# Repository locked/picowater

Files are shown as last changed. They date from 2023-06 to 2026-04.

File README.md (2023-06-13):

cd build

cmake -DPICO_BOARD=pico_w -DWIFI_SSID="<wifi>" -DWIFI_PASSWORD="<secret>" -DSERVER_IP="<ip>" -DSERVER_PORT=<port> ..

make

# Sources

https://github.com/iiot2k/pico-lib2/blob/main/src/dev/dev_ds3231/dev_ds3231.c

https://ghubcoder.github.io/posts/awaking-the-pico/

https://github.com/ghubcoder/PicoSleepRtc/blob/master/ds3232rtc.cpp

https://github.com/raspberrypi/pico-examples/blob/master/adc/hello_adc/hello_adc.c

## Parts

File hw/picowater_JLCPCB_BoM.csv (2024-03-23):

Comment | Designator | Footprint | LCSC
220 | R9,R3 | R_0402_1005Metric | C2909336
LED | D4 | LED_0603_1608Metric_Pad1.05x0.95mm_HandSolder | None
1N4007 | D3 | D_SOD-123 | C3018540
TLP160G | U5 | MFSOP6-4_4.4x3.6mm_P1.27mm | C2848498
NCP1117 | U4 | SOT-223-3_TabPin2 | C17314
10u | C4,C5 | C_0805_2012Metric | C88484
SN74HC74N | U2 | SOIC-14_3.9x8.7mm_P1.27mm | C6762
10K | R5,R8,R6,R7 | R_0402_1005Metric | C25744
100nF | C1,C3 | C_0402_1005Metric | C1525
22pF | C2 | C_0402_1005Metric | C1555
34K | R2 | R_0402_1005Metric | C48939
PCF8563T | U3 | SOIC-8_3.9x4.9mm_P1.27mm | C7440
100 | R10 | R_0402_1005Metric | C2906884
JST-PH2 Bat | J6 | JST_PH_S2B-PH-SM4-TB_1x02-1MP_P2.00mm_Horizontal | C295747
100K | R4,R1 | R_0402_1005Metric | C25741
S8050 | Q1 | TSOT-23 | C909746
1A 20V Schottky | D1 | D_SOD-123F | C169527

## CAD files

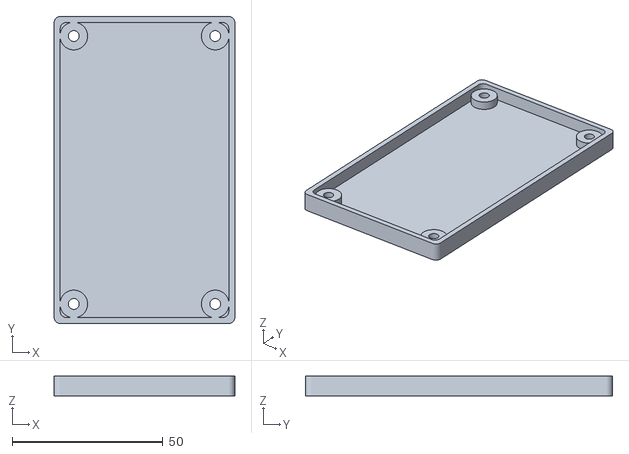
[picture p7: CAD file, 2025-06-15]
case/bottom.stl
60.0 x 102.0 x 6.60

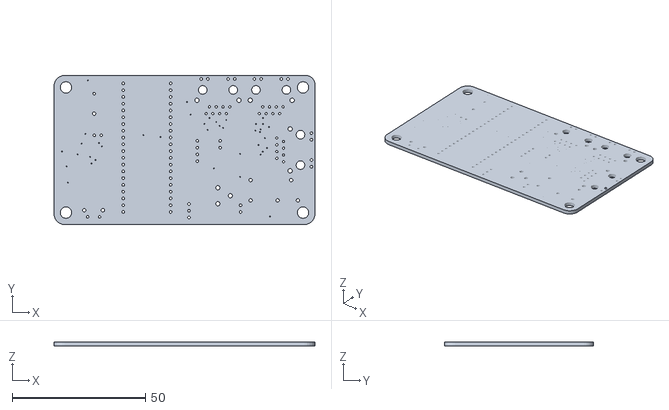
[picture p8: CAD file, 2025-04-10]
hw/picowater.stl
98.0 x 56.0 x 1.51

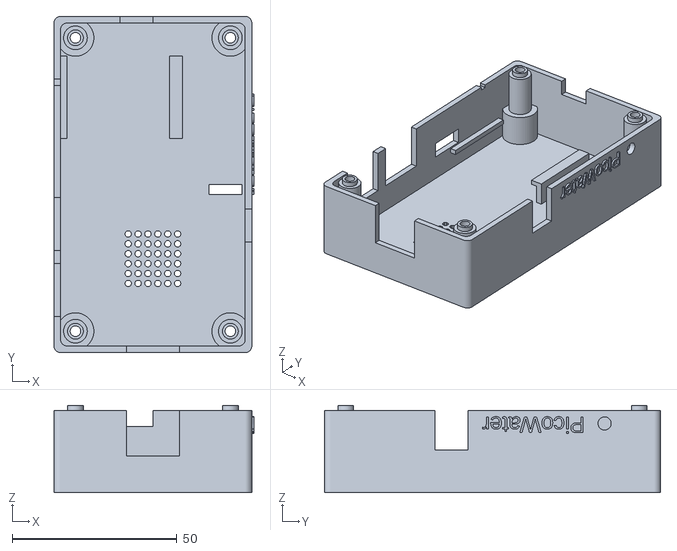
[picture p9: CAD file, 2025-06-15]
case/top.stl
60.7 x 102.0 x 26.5

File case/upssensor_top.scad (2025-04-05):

include <common.scad>;

module case () {
    difference () {
        minkowski() {
            cube([height-round_radius*2, width-round_radius*2, top_depth]);
            cylinder(r=round_radius, h=0.0001);
        }

        translate([round_radius,round_radius,thickness]) minkowski() {
            cube([pcb_height-round_radius*2, pcb_width-round_radius*2, top_depth]);
            cylinder(r=round_radius, h=1);
        }
    }

    // Screw supports
    for (hole = holes) {
        translate([hole[0], hole[1], hole[2]+top_depth])
            cylinder(r=pcb_screw_hole_radius-0.1, h=1.5);
        translate(hole)
            cylinder(r=screw_hole_radius+2, h=top_depth);
        translate(hole)
            cylinder(r=screw_hole_radius+4, h=6);
    }

    translate([pcb_height+thickness, pcb_width-20, top_depth-2])
    rotate([90, 180, 90])
    linear_extrude(thickness/3)
    text("PicoWater", size=6);
}

module screw_holes() {
    for (hole = holes) {
        translate([hole[0], hole[1], -thickness])
            cylinder(r=screw_hole_radius, h=top_depth+thickness+1.5);
        translate([hole[0], hole[1], -bottom_depth+thickness])
            cylinder(r=3.5, h=bottom_depth-thickness+2.5);
    }
}

module rj45() {
    rj45_posx = pcb_height / 2 - rj45[0] / 2;
    rj45_posz = top_depth - rj45[2] + 0.001;
    translate([rj45_posx, -thickness, rj45_posz]) cube(rj45);
}

module debug_hole() {
    debug_posx = pcb_height + thickness;
    debug_posy = pcb_width - 13;
    debug_posz = top_depth - 4;
    translate([debug_posx, debug_posy, debug_posz]) rotate([0, -90, 0]) cylinder(r=2, h=thickness);
}

module airvents() {
    rad = 1;
    posx = pcb_height / 2 - (5*rad*3/2);
    posy = pcb_width / 2 - 5*rad;
    for (i = [0,1,2,3,4,5]) {
        for (j = [0,1,2,3,4,5]) {
            translate([posx + i*rad*3, posy + j*rad*3, 0])
                cylinder(r=rad, h=thickness, $fn=10);
        }
    }
}

module uart() {
    uart_posx = pcb_height - thickness - 2;
    uart_posy = pcb_width - thickness - 10 - 15;
    translate([uart_posx, uart_posy, 0])
        cube([3, 10, thickness]);
}

difference () {
    case();
    screw_holes();
    rj45();
    debug_hole();
    airvents();
    uart();
}

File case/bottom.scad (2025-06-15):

include <common.scad>;

module case () {
    difference () {
        minkowski() {
            cube([height-round_radius*2, width-round_radius*2, bottom_depth]);
            cylinder(r=round_radius, h=pcb_thickness);
        }

        translate([round_radius,round_radius,thickness]) minkowski() {
            cube([pcb_height-round_radius*2, pcb_width-round_radius*2, bottom_depth]);
            cylinder(r=round_radius, h=1);
        }
    }

    // Screw supports
    for (hole = holes) {
        translate(hole)
            cylinder(r=screw_hole_radius+3, h=bottom_depth);
    }
}

module screw_holes() {
    for (hole = holes) {
        translate([hole[0], hole[1], -thickness])
            cylinder(r=screw_hole_radius+0.2, h=bottom_depth+thickness);

        translate([hole[0], hole[1], -bottom_depth+thickness])
            cylinder(r=3.3, h=bottom_depth-thickness+3, $fn=6);
    }
}

difference () {
    case();
    screw_holes();
}

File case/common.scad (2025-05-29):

pcb_width = 98;
pcb_height = 56;
pcb_thickness = 1.6;
pcb_screw_hole_radius = 2.4;	// M4/2-margin

thickness = 2;
round_radius = 2;

width = pcb_width + thickness * 2;	// y
height = pcb_height + thickness * 2;	// x
bottom_depth = 5;	// z
top_depth = 25;		// z

screw_hole_radius = 1.6;	// M2/2
screw_posx = 4.5;
screw_posy = 4.5;

rj45 = [16, thickness*2, 13.8];
powerjack = [10, thickness*2, 12];

$fn = 50;

posx = screw_posx;
posy = screw_posy;
holes = [
    [posx, posy, 0],
    [pcb_height-posx, posy, 0],
    [posx, pcb_width-posy, 0],
    [pcb_height-posx, pcb_width-posy, 0]
];

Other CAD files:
case/top.scad

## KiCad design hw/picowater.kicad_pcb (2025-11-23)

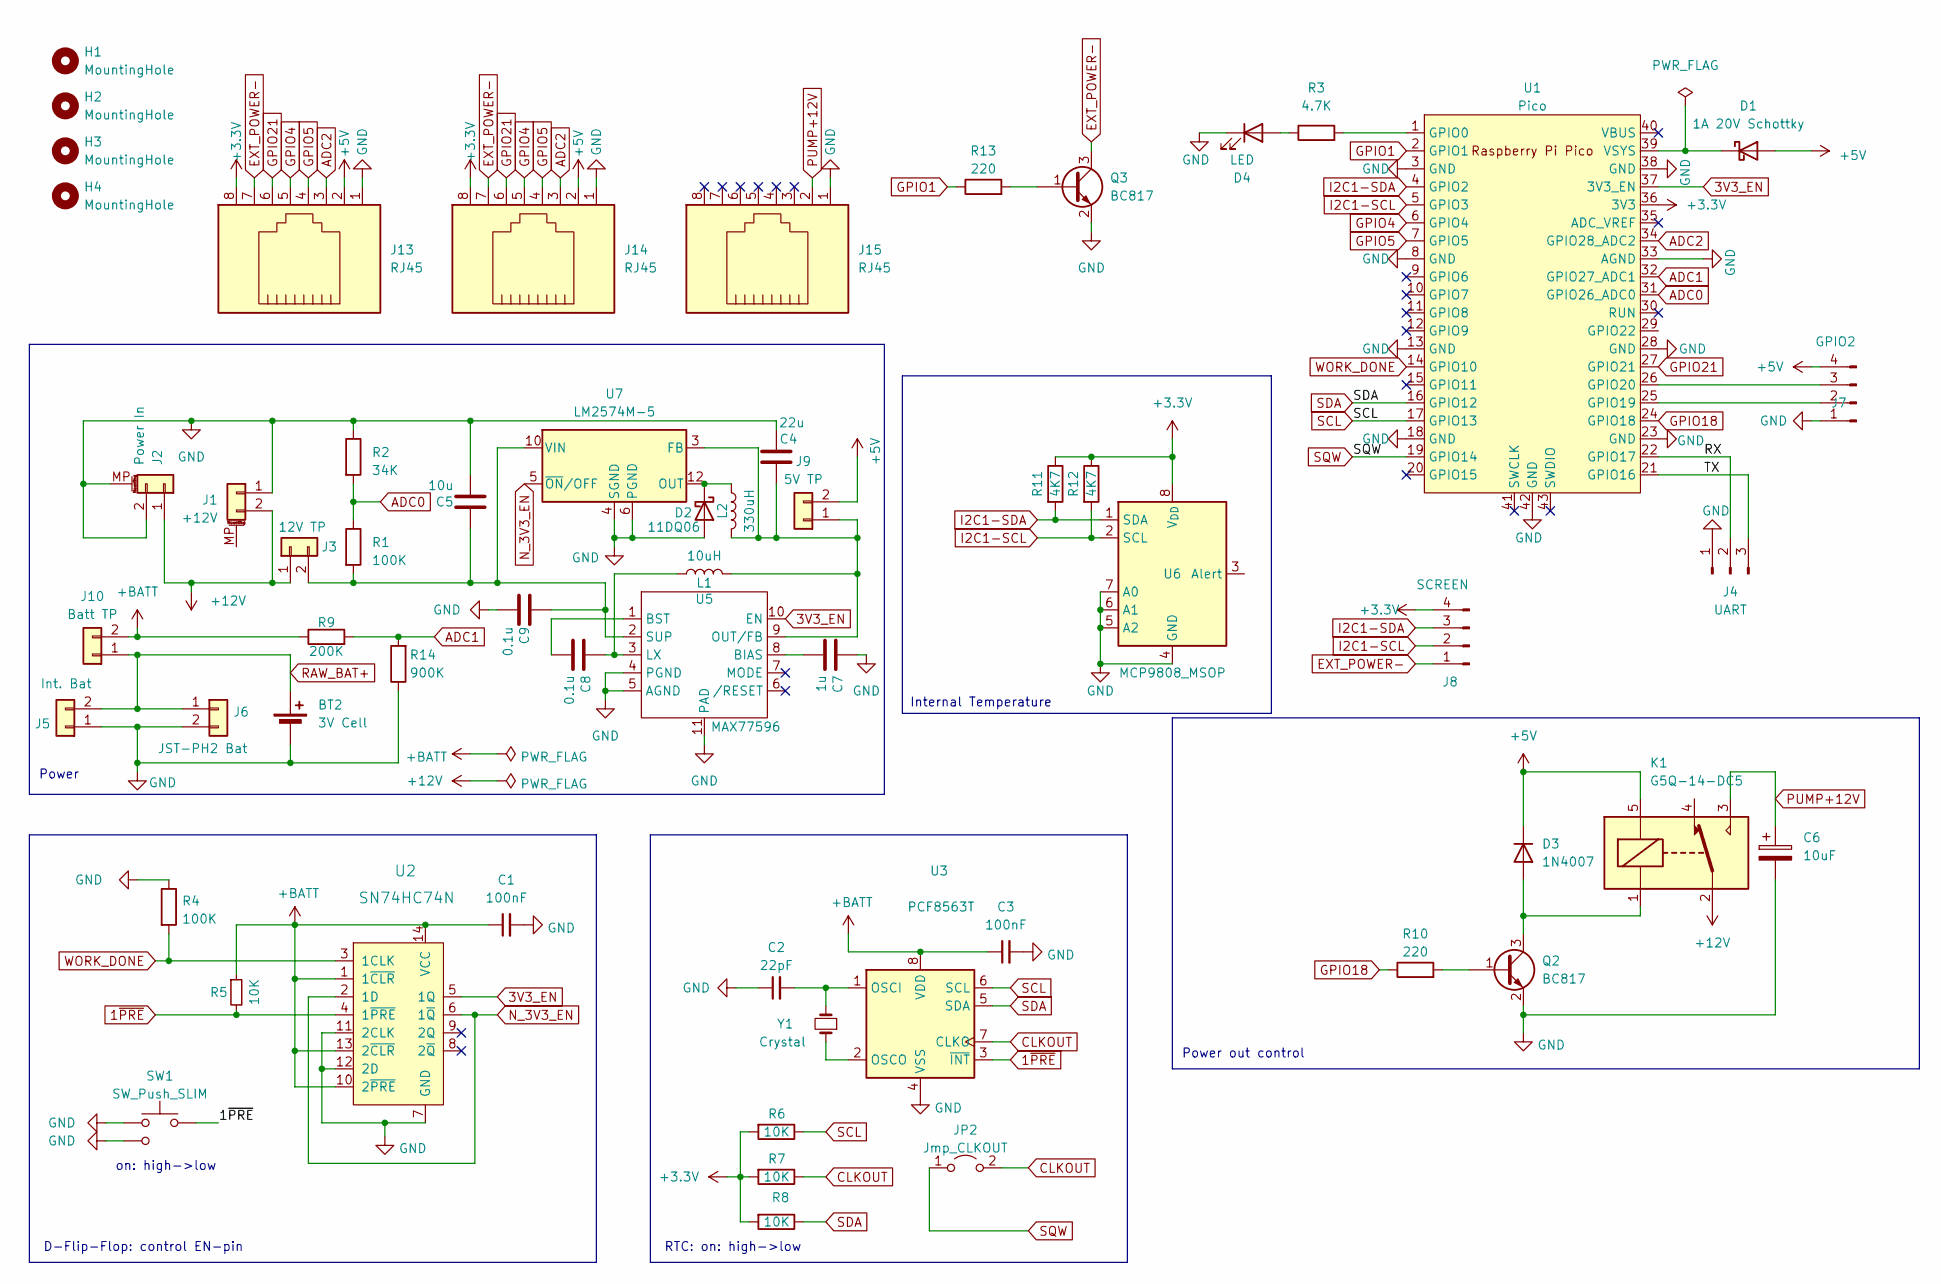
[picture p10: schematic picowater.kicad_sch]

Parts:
BT2: 3V Cell; MPD_BC501SM-TR_custom
C1, C3: 100nF; C_0402_1005Metric; LCSC C1525
C2: 22pF; C_0402_1005Metric; LCSC C1555
C4: 22u; C_0805_2012Metric; LCSC C2846677
C5: 10u; C_0805_2012Metric; LCSC C2846677
C6: 10uF; CP_Radial_D8.0mm_P3.80mm
C7: 1u; C_0603_1608Metric
C8, C9: 0.1u; C_0603_1608Metric
D1: 1A 20V Schottky; D_SOD-123F; LCSC C169527
D2: 11DQ06
D3: 1N4007; D_SOD-123; LCSC C3018540
D4: LED; LED_0603_1608Metric_Pad1.05x0.95mm_HandSolder; JLCPCB Part Number C72041
H1, H2, H3, H4: MountingHole; hole_5mm
J1: +12V; PinSocket_1x02_P2.54mm_Vertical
J2: Power In; BarrelJack_CUI_PJ-102AH_Horizontal
J3: 12V TP; PinHeader_1x02_P2.54mm_Vertical
J4: UART; PinHeader_1x03_P2.54mm_Vertical
J5: Int. Bat; PinHeader_1x02_P2.54mm_Vertical; LCSC C295747
J6: JST-PH2 Bat; JST_PH_S2B-PH-SM4-TB_1x02-1MP_P2.00mm_Horizontal; LCSC C295747
J7: GPIO2; PinHeader_1x04_P2.54mm_Vertical
J8: SCREEN; PinHeader_1x04_P2.54mm_Vertical
J9: 5V TP; PinHeader_1x02_P2.54mm_Vertical
J10: Batt TP; PinHeader_1x02_P2.54mm_Vertical
J13, J14, J15: RJ45; RJ45_BEL_SS74301-00x_Vertical
JP2: Jmp_CLKOUT; SolderJumper-2_P1.3mm_Open_Pad1.0x1.5mm
K1: G5Q-14-DC5; Relay_SPDT_Omron-G5Q-1
L1: 10uH; C_0805_2012Metric
L2: 330uH
Q2, Q3: BC817; SOT-23
R1, R4: 100K; R_0402_1005Metric; LCSC C25741
R2: 34K; R_0402_1005Metric; LCSC C48939
R3: 4.7K; R_0402_1005Metric
R5, R6, R8: 10K; R_0402_1005Metric; LCSC C25744
R7: 10K; R_0805_2012Metric; LCSC C25744
R9: 200K; R_0402_1005Metric
R10, R13: 220; R_0402_1005Metric; LCSC C2909336
R11, R12: 4K7; C_0603_1608Metric; LCSC C25900
R14: 900K; R_0402_1005Metric
SW1: SW_Push_SLIM; SW_Tactile_SPST_Angled_PTS645Vx31-2LFS
U1: Pico; RPi_Pico_SMD_TH
U2: SN74HC74N; SO-14_5.3x10.2mm_P1.27mm; MPN SN74HC74N; Digi-Key_PN 296-1602-5-ND
U3: PCF8563T; SOIC-8_3.9x4.9mm_P1.27mm; LCSC C7440
U5: MAX77596; TDFN-10-EP_2.5mm
U6: MCP9808_MSOP; MSOP-8_3x3mm_P0.65mm; LCSC C129490
U7: LM2574M-5
Y1: Crystal; Crystal_SMD_3215-2Pin_3.2x1.5mm; LCSC C32346

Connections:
1~PRE: R5.2, SW1.2, U2.4 (1~PRE), U3.3 (~INT)
3V3_EN: U1.37 (3V3_EN), U2.5 (1Q), U5.10 (EN)
+3.3V: J8.4, J13.8, J14.8, R6.2, R7.2, R8.2, R11.1, R12.1, U1.36 (3V3), U6.8 (V_{DD})
+5V: D1.2 (A), D3.1 (K), J7.4, J9.2, J13.2, J14.2, K1.5
+12V: J1.2, J2.1, J3.1, K1.2
+BATT: C1.1, C3.1, J10.2, R5.1, R9.1, U2.1 (1~CLR), U2.10 (2~PRE), U2.13 (2~CLR), U2.14 (VCC), U3.8 (VDD)
/RX: J4.2, U1.22 (GPIO17)
/TX: J4.3, U1.21 (GPIO16)
ADC0: R1.1, R2.2, U1.31 (GPIO26_ADC0)
ADC1: R9.2, R14.2, U1.32 (GPIO27_ADC1)
ADC2: J13.3, J14.3, U1.34 (GPIO28_ADC2)
CLKOUT: JP2.2 (B), R7.1, U3.7 (CLKO)
EXT_POWER-: J8.1, J13.7, J14.7, Q3.3 (C)
GND: BT2.2 (-), C1.2, C2.1, C3.2, C4.2, C5.2, C6.2, C7.1, C9.2, D2.2 (A), D4.1 (K), J1.1, J2.2, J2.MP (MountPin), J4.1, J5.1, J6.2, J7.1, J13.1, J14.1, J15.1, Q2.2 (E), Q3.2 (E), R2.1, R4.1, R14.1, SW1.1, SW1.3 (1), U1.3 (GND), U1.8 (GND), U1.13 (GND), U1.18 (GND), U1.23 (GND), U1.28 (GND), U1.33 (AGND), U1.38 (GND), U1.42 (GND), U2.7 (GND), U2.11 (2CLK), U2.12 (2D), U3.4 (VSS), U5.4 (PGND), U5.5 (AGND), U5.11 (PAD), U6.4 (GND), U6.5 (A2), U6.6 (A1), U6.7 (A0), U7.4 (SGND), U7.6 (PGND)
GPIO1: R13.1, U1.2 (GPIO1)
GPIO4: J13.5, J14.5, U1.6 (GPIO4)
GPIO5: J13.4, J14.4, U1.7 (GPIO5)
GPIO18: R10.1, U1.24 (GPIO18)
GPIO21: J13.6, J14.6, U1.27 (GPIO21)
I2C1-SCL: J8.2, R12.2, U1.5 (GPIO3), U6.2 (SCL)
I2C1-SDA: J8.3, R11.2, U1.4 (GPIO2), U6.1 (SDA)
N_3V3_EN: U2.2 (1D), U2.6 (1~Q), U7.5 (~ON/OFF)
unnamed: D1.1 (K), U1.39 (VSYS)
unnamed: D2.1 (K), L2.1, U7.12 (OUT)
unnamed: D3.2 (A), K1.1, Q2.3 (C)
unnamed: D4.2 (A), R3.1
unnamed: C5.1, C9.1, J3.2, R1.2, U5.2 (SUP), U7.10 (VIN)
unnamed: J7.2, U1.25 (GPIO19)
unnamed: J7.3, U1.26 (GPIO20)
unnamed: C4.1, J9.1, L1.2, L2.2, U5.9 (OUT/FB), U7.3 (FB)
unnamed: Q2.1 (B), R10.2
unnamed: Q3.1 (B), R13.2
unnamed: R3.2, U1.1 (GPIO0)
unnamed: C2.2, U3.1 (OSCI), Y1.2
unnamed: U3.2 (OSCO), Y1.1
unnamed: C7.2, U5.8 (BIAS)
unnamed: C8.2, U5.1 (BST)
unnamed: C8.1, L1.1, U5.3 (LX)
PUMP+12V: C6.1, J15.2, K1.3
RAW_BAT+: BT2.1 (+), J5.2, J6.1, J10.1
SCL: R6.1, U1.17 (GPIO13), U3.6 (SCL)
SDA: R8.1, U1.16 (GPIO12), U3.5 (SDA)
SQW: JP2.1 (A), U1.19 (GPIO14)
WORK_DONE: R4.2, U1.14 (GPIO10), U2.3 (1CLK)

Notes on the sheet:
Power
on: high->low
Power out control
RTC: on: high->low
D-Flip-Flop: control EN-pin
Internal Temperature

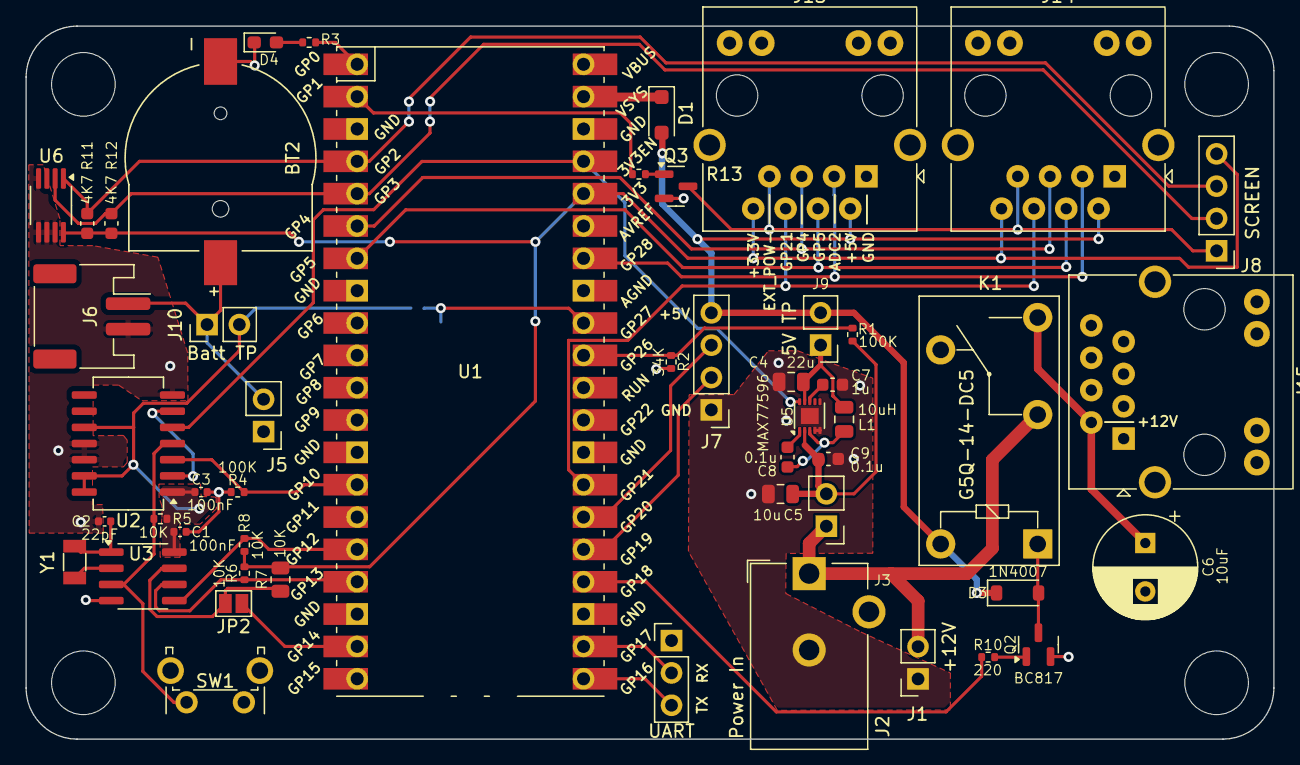
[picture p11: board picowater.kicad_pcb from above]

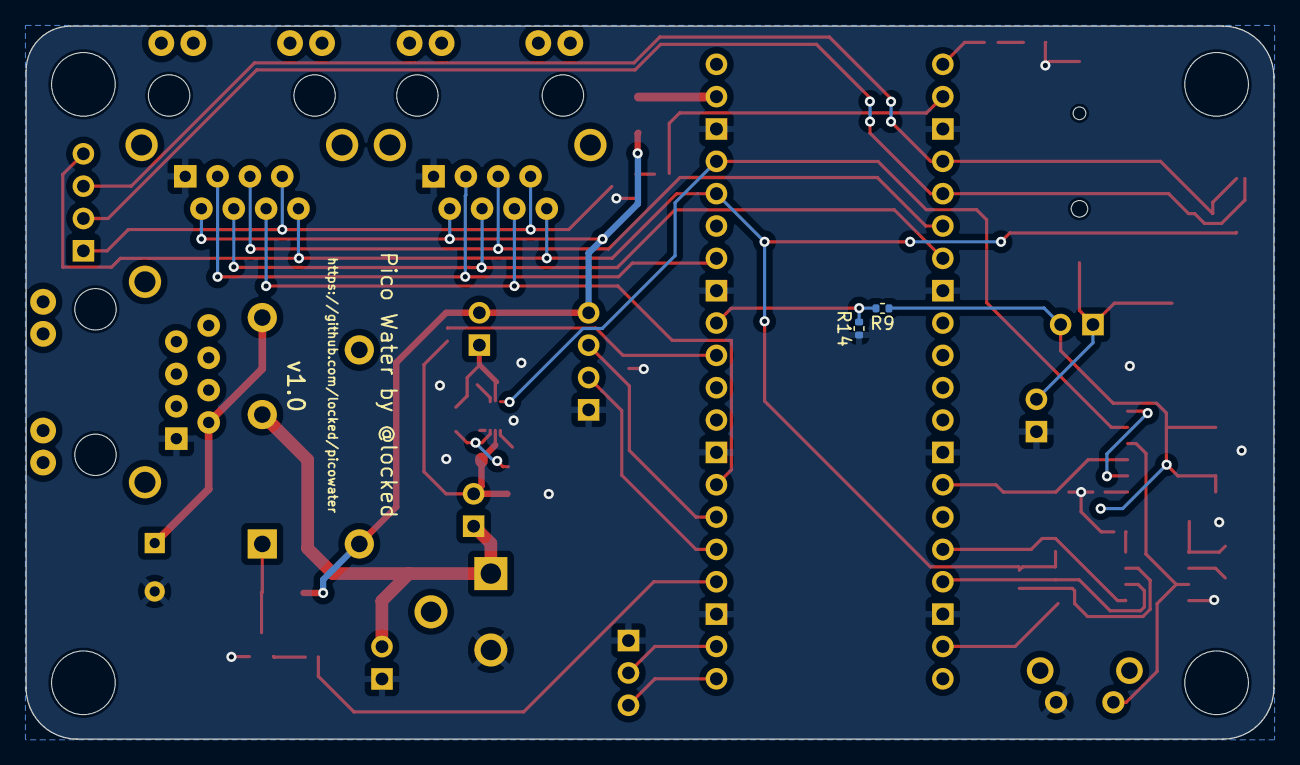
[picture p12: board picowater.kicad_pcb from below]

Board: 2 copper layers, 98.0 x 56.0 mm, 56 parts (2 on the bottom side), 43 nets.

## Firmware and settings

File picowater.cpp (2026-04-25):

#include <stdlib.h>
#include <stdio.h>
#include <string.h>
#include <time.h>

#include "pico/stdlib.h"
#include "pico/sleep.h"

#include "hardware/rtc.h"
#include "hardware/uart.h"
#include "hardware/gpio.h"
#include "hardware/adc.h"
#include "hardware/i2c.h"
#include "hardware/watchdog.h"

#include "pico/util/datetime.h"

#include "hardware/clocks.h"
#include "hardware/rosc.h"
#include "hardware/structs/scb.h"

#include "wifi.h"

#include "ssd1306.h"
#include "acme_5_outlines_font.h"
#include "bubblesstandard_font.h"
#include "crackers_font.h"
#include "BMSPA_font.h"

#include "pcf8563/pcf8563.h"
#include "mcp9808/mcp9808.h"

#include "network.h"

#include "picowater.h"


int pump_force_ms;
bool wakeup_everymin;

int dist;
float batlvl;
float batlvl2;
float systemp;


void _i2c_init(i2c_inst_t* i2c, uint32_t sda, uint32_t scl, uint32_t baudrate) {
	uint8_t idx = (i2c == i2c0) ? 0 : 1;

	i2c_init(i2c, baudrate);

	// init pins
	gpio_set_function(sda, GPIO_FUNC_I2C);
	gpio_set_function(scl, GPIO_FUNC_I2C);

	gpio_pull_up(sda);
	gpio_pull_up(scl);
}



void blink(int count, int delay) {
	int i = 0;
	gpio_put(LED_PIN, 0);
	while (i < count) {
		gpio_put(LED_PIN, 1);
		sleep_ms(20);
		gpio_put(LED_PIN, 0);
		sleep_ms(delay);
		i++;
	}
}


void setup_i2c() {
	i2c_init(i2c1, 400000);
	gpio_set_function(SCREEN_SDA_PIN, GPIO_FUNC_I2C);
	gpio_set_function(SCREEN_SCL_PIN, GPIO_FUNC_I2C);
	gpio_pull_up(SCREEN_SDA_PIN);
	gpio_pull_up(SCREEN_SCL_PIN);
}


void setup_screen(ssd1306_t *disp) {
	disp->external_vcc = false;
	ssd1306_init(disp, 128, 64, 0x3C, i2c1);
	ssd1306_clear(disp);
}


void setup_adc() {
	uart_puts(UART_ID, "== Setup ADC ==\r\n");
	uart_default_tx_wait_blocking();
	printf("== Setup ADC ==\n");
	adc_init();
	// Make sure GPIO is high-impedance, no pullups etc
	adc_gpio_init(BATTERY_ADC_PIN);
	adc_gpio_init(BATTERY2_ADC_PIN);
	adc_gpio_init(HUMIDITY_ADC_PIN);
}


void setup_rtc_pcf() {
	uart_puts(UART_ID, "== RTC PCF8563 init ==\r\n");
	uart_default_tx_wait_blocking();
	printf("RTC PCF8563 init\n");

	//_i2c_init(I2C_RTC_PORT, RTC_SDA_PIN, RTC_SCL_PIN, 100000);
	i2c_init(I2C_RTC_PORT, 100 * 1000);
	gpio_set_function(RTC_SDA_PIN, GPIO_FUNC_I2C);
	gpio_set_function(RTC_SCL_PIN, GPIO_FUNC_I2C);
	gpio_pull_up(RTC_SDA_PIN);
	gpio_pull_up(RTC_SCL_PIN);

	pcf8563_set_i2c(I2C_RTC_PORT);
	printf("[picoclock] pcf8563_set_i2c OK\r\n");

	time_struct _dt = pcf8563_getDateTime();
	if (!_dt.volt_low) {
		printf("RTC not initialized [%d] %d-%d-%d %d:%d:%d\n", _dt.century, _dt.year, _dt.month, _dt.day, _dt.hour, _dt.min, _dt.sec);

		// Fetch date
		//network_update();
	}
}

void rtc_pcf_sleep() {
	printf("Will set ALARM\n");
	uart_default_tx_wait_blocking();
	sleep_ms(500);

	time_struct dt = pcf8563_getDateTime();
	int min = dt.min;
	int hour = dt.hour;
	int day = dt.day;
	int weekday = dt.weekday;

	if (wakeup_everymin) {
		min += 1;
		if (min > 59) {
			hour += 1;
			min -= 60;
		}
	} else {
		hour += 1;
	}
	if (hour > 23) {
		day += 1;
		weekday += 1;
		hour -= 24;
	}
	if (day > 30) {
		day -= 30;
	}
	if (weekday > 6) {
		weekday = 0;
	}

	printf("Set ALARM to day %02d at %02d:%02d weekday:%d\n", day, hour, min, weekday);
	uart_default_tx_wait_blocking();
	sleep_ms(100);

	pcf8563_setAlarm(min, hour, day, weekday);
	pcf8563_enableAlarm();

	// shutdown PI through SN74HC74N
	blink(2, 500);
	printf("SHUTDOWN\n");
	uart_default_tx_wait_blocking();
	sleep_ms(100);
	gpio_put(RTC_WORK_DONE_PIN, 1);
}


void setup_humidity() {
	gpio_init(HUMIDITY_POWER_PIN);
	gpio_set_dir(HUMIDITY_POWER_PIN, GPIO_OUT);
}


void setup_distance() {
	gpio_init(DISTANCE_ECHO_PIN);
	gpio_init(DISTANCE_TRIG_PIN);
	gpio_set_dir(DISTANCE_TRIG_PIN, GPIO_OUT);
	gpio_set_dir(DISTANCE_ECHO_PIN, GPIO_IN);
	gpio_pull_down(DISTANCE_ECHO_PIN);
}

int measure_distance() {
	absolute_time_t pulse_start, pulse_end;
	uint32_t loop_count = 0;
	uint32_t loop_count2 = 0;
	gpio_put(DISTANCE_TRIG_PIN, 0);
	sleep_ms(200);
	gpio_put(DISTANCE_TRIG_PIN, 1);
	sleep_us(10);
	gpio_put(DISTANCE_TRIG_PIN, 0);
	while (gpio_get(DISTANCE_ECHO_PIN) == 0) {
		if (loop_count++ > 3000000) {
			printf("exit loop\r\n");
			break;
		}
	}
	//tight_loop_contents();
	pulse_start = get_absolute_time();
	while (gpio_get(DISTANCE_ECHO_PIN) == 1) {
		sleep_us(1);
		loop_count2++;
		if (loop_count2 > 30000) {
			printf("exit loop2\r\n");
			break;
		}
	}
	pulse_end = get_absolute_time();
	int64_t pulse_duration = absolute_time_diff_us(pulse_start, pulse_end);
	int distance = pulse_duration / 29 / 2;
	char buf[100] = "";
	sprintf(buf, "distance:[%d] loop_count:[%u/%u] pulse_start:[%u] pulse_end:[%u] pulse_duration:[%l]\r\n", distance, loop_count, loop_count2, pulse_start, pulse_end, pulse_duration);
	uart_puts(UART_ID, buf);
	uart_default_tx_wait_blocking();
	printf(buf);
	return distance;
}

void add_water(datetime_t *dt) {
	char buf[100] = "";
	// Read Main Battery ADC
	adc_select_input(0); // Select ADC input 0 (GPIO26)
	const float conversion_factor = 3.3f / (1 << 12);
	batlvl = adc_read() * conversion_factor;

	// Read Battery2 ADC
	adc_select_input(1); // Select ADC input 1 (GPIO27)
	batlvl2 = adc_read() * conversion_factor;

	// Read Humidity ADC
	/*adc_select_input(2); // Select ADC input 2 (GPIO28)
	gpio_put(HUMIDITY_POWER_PIN, 1);
	sleep_ms(10);
	float humidity_result = adc_read() * conversion_factor;
	gpio_put(HUMIDITY_POWER_PIN, 0);
	sprintf(buf, "ADC Battery:[%fV] Battery2:[%fV] Humidity:[%fV]\r\n", batlvl, batlvl2, humidity_result);
	uart_puts(UART_ID, buf);
	uart_default_tx_wait_blocking();
	printf(buf);*/

	// Temperature
	systemp = mcp9808_get_temperature();

	watchdog_update();
	// Water level
	dist = measure_distance();
	if (dist <= 0) {
		printf("Failed getting distance:[%d]\r\n", dist);
		sleep_ms(1000);
		dist = measure_distance();
	}
	sprintf(buf, "DIST:[%u]\r\n", dist);
	uart_puts(UART_ID, buf);
	uart_default_tx_wait_blocking();
	printf(buf);
	watchdog_update();

	// shutdown power for ext devices (except pump)
	gpio_put(EXT_POWER_PIN, 0);

	// Decide to activate pump or not
	int activate_pump_ms = 0;
	// Every hour:
	//int factor = 1;
	//if (dt->hour >= 8 && dt->hour <= 21) {
	// Morning and evening:
	/*int factor = 2;
	if (dt->hour == 8 || dt->hour == 21) {
		sprintf(buf, "In time for pump:[%d]\r\n", dt->hour);
		uart_puts(UART_ID, buf);
		uart_default_tx_wait_blocking();
		printf(buf);
		if (dist >= 1 && dist <= 18) {
			sprintf(buf, "Enough water for pump:[%d]\r\n", dist);
			uart_puts(UART_ID, buf);
			uart_default_tx_wait_blocking();
			printf(buf);
			if (humidity_result >= 2.5) {
				// Very dry
				activate_pump_ms = 10000 * factor;
			} else if (humidity_result >= 2.25) {
				// A bit dry
				activate_pump_ms = 7500 * factor;
			} else if (humidity_result >= 1.75) {
				// Not very dry
				activate_pump_ms = 5000 * factor;
			}
		}
	}*/

	//bool wakeup_everymin = false;

	// WIFI
	bool enable_wifi = true;
	if (enable_wifi) {
		blink(3, 100);
		sleep_ms(1000);

		int network_rc = network_update();
		watchdog_update();

		printf("wakeup_everymin:[%d] activate_pump_ms:[%d] network_rc:[%d]\n", wakeup_everymin, activate_pump_ms, network_rc);
		if (network_rc > 0) {
			// Network failed, check if manual failsafe necessary
			activate_pump_ms = 0;
			if ((dt->hour == 7 || dt->hour == 20) && batlvl > 2.9 && dist > 10) {
				// It's time AND we have enough battery and water, activate pump
				activate_pump_ms = 10000;
			}
		} else {
			activate_pump_ms = pump_force_ms;
		}
	}


	// Pump activation
	if (activate_pump_ms > 0) {
		blink(5, 100);

		sprintf(buf, "Activate pump for [%dms]\r\n", activate_pump_ms);
		uart_puts(UART_ID, buf);
		uart_default_tx_wait_blocking();
		printf(buf);

		gpio_put(PUMP_PIN, 1);
		// Loop because we want to update watchdog every 500ms
		for (int sum_ms = 0; sum_ms<activate_pump_ms; sum_ms+=500) {
			sleep_ms(500);
			watchdog_update();
		}
		gpio_put(PUMP_PIN, 0);
	}
	watchdog_update();

	printf("add_water DONE\n");
}


int main() {
	char buf[50] = "";

	uart_init(UART_ID, BAUD_RATE);
	gpio_set_function(UART_TX_PIN, GPIO_FUNC_UART);
	gpio_set_function(UART_RX_PIN, GPIO_FUNC_UART);

	uint scb_orig = scb_hw->scr;
	uint clock0_orig = clocks_hw->sleep_en0;
	uint clock1_orig = clocks_hw->sleep_en1;

	gpio_init(LED_PIN);
	gpio_set_dir(LED_PIN, GPIO_OUT);
	gpio_put(LED_PIN, 1);

	gpio_init(RTC_WORK_DONE_PIN);
	gpio_set_dir(RTC_WORK_DONE_PIN, GPIO_OUT);
	gpio_put(RTC_WORK_DONE_PIN, 0);

	gpio_init(EXT_POWER_PIN);
	gpio_set_dir(EXT_POWER_PIN, GPIO_OUT);
	gpio_put(EXT_POWER_PIN, 1);

	gpio_init(PUMP_PIN);
	gpio_set_dir(PUMP_PIN, GPIO_OUT);
	gpio_put(PUMP_PIN, 0);

	uart_puts(UART_ID, "==START==\r\n");
	uart_default_tx_wait_blocking();
	stdio_init_all();
	printf("==START==\n");

	gpio_pull_up(RTC_SQW_PIN);

	// Setup I2C
	setup_i2c();

	//ssd1306_t disp;
	//setup_screen(&disp);
	//ssd1306_draw_line(&disp, 0, 0, 127, 0);
	//sprintf(buf, "start");
	//ssd1306_draw_string_with_font(&disp, 1, 1, 2, acme_font, buf);
	//ssd1306_show(&disp);

	watchdog_enable(10000, false);

	// Setup humidity sensor
	setup_humidity();

	// Init water level
	setup_distance();

	// ADC
	setup_adc();

	// RTC
	setup_rtc_pcf();
	watchdog_update();

	gpio_put(LED_PIN, 0);

	datetime_t dt;
	char datetime_buf[256];
	char *datetime_str = &datetime_buf[0];
	uart_puts(UART_ID, "Start loop\r\n");
	uart_default_tx_wait_blocking();
	while (1) {
		//blink(1, 100);
		//sleep_ms(1000);

		add_water(&dt);

		printf("sleep\n");
		rtc_pcf_sleep();
		sleep_ms(500);
		uint32_t sleep_for = wakeup_everymin ? 60000 : 3600000;
		printf("sleep done (should never be seen) => start work around with sleep(%d)\n", sleep_for);
		sleep_ms(sleep_for);
	}
	return 0;
}

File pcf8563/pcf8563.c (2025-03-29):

#include "pcf8563.h"

#include "pico/stdlib.h"


uint8_t constrain(uint8_t x, uint8_t a, uint8_t b){
  if (x < a) {
    return a;
  }
  if (x > b) {
    return b;
  }

  return x;
}


/*
 * Wire abstraction
 */

i2c_inst_t *pcf8563_i2c;

void pcf8563_set_i2c(i2c_inst_t *i2c) {
	pcf8563_i2c = i2c;
}


/* Private internal functions, but useful to look at if you need a similar func. */
uint8_t pcf8563_decToBcd(uint8_t val) {
    return ( (val/10*16) + (val%10) );
}

uint8_t pcf8563_bcdToDec(uint8_t val) {
    return ( (val/16*10) + (val%16) );
}

void pcf8563_zeroClock() {
    uint8_t txBuffer[256];
    uint32_t usedTxBuffer;
    txBuffer[usedTxBuffer++] = (uint8_t)0x0;        // start address

    txBuffer[usedTxBuffer++] = (uint8_t)0x0;     //control/status1
    txBuffer[usedTxBuffer++] = (uint8_t)0x0;     //control/status2
    txBuffer[usedTxBuffer++] = (uint8_t)0x00;    //set seconds to 0 & VL to 0
    txBuffer[usedTxBuffer++] = (uint8_t)0x00;    //set minutes to 0
    txBuffer[usedTxBuffer++] = (uint8_t)0x00;    //set hour to 0
    txBuffer[usedTxBuffer++] = (uint8_t)0x01;    //set day to 1
    txBuffer[usedTxBuffer++] = (uint8_t)0x00;    //set weekday to 0
    txBuffer[usedTxBuffer++] = (uint8_t)0x81;    //set month to 1, century to 1900
    txBuffer[usedTxBuffer++] = (uint8_t)0x00;    //set year to 0
    txBuffer[usedTxBuffer++] = (uint8_t)0x80;    //minute alarm value reset to 00
    txBuffer[usedTxBuffer++] = (uint8_t)0x80;    //hour alarm value reset to 00
    txBuffer[usedTxBuffer++] = (uint8_t)0x80;    //day alarm value reset to 00
    txBuffer[usedTxBuffer++] = (uint8_t)0x80;    //weekday alarm value reset to 00
    txBuffer[usedTxBuffer++] = (uint8_t)SQW_32KHZ; //set SQW to default, see: setSquareWave
    txBuffer[usedTxBuffer++] = (uint8_t)0x0;     //timer off

    if (i2c_write_blocking_until(pcf8563_i2c, RTCC_ADDR, txBuffer, usedTxBuffer, false, make_timeout_time_ms(1000)) == PICO_ERROR_GENERIC){
		printf("pcf8563_zeroClock write error\n");
    }
}

void pcf8563_clearStatus() {
    uint8_t txBuffer[256];
    uint32_t usedTxBuffer;
    txBuffer[usedTxBuffer++] = (uint8_t)0x0;
    txBuffer[usedTxBuffer++] = (uint8_t)0x0;                 //control/status1
    txBuffer[usedTxBuffer++] = (uint8_t)0x0;                 //control/status2
    if (i2c_write_blocking_until(pcf8563_i2c, RTCC_ADDR, txBuffer, usedTxBuffer, false, make_timeout_time_ms(1000)) == PICO_ERROR_GENERIC){
		printf("pcf8563_clearStatus write error\n");
    }
}

/*
* Read status byte
*/
uint8_t pcf8563_readStatus2() {
    time_struct t = pcf8563_getDateTime();
    return t.status2;
}

void pcf8563_clearVoltLow(void) {
    time_struct t = pcf8563_getDateTime();
    // Only clearing is possible on device (I tried)
    pcf8563_setDateTime(t.day, t.weekday, t.month,
                t.century, t.year, t.hour,
                t.min, t.sec);
}


/*
* Atomicly read all device registers in one operation
*/
time_struct pcf8563_getDateTime(void) {
    time_struct t;

    /* Start at beginning, read entire memory in one go */
    uint8_t txBuffer[256];
    uint32_t usedTxBuffer;
    txBuffer[usedTxBuffer++] = (uint8_t)RTCC_STAT1_ADDR;
    if (i2c_write_blocking_until(pcf8563_i2c, RTCC_ADDR, txBuffer, usedTxBuffer, false, make_timeout_time_ms(1000)) == PICO_ERROR_GENERIC){
		printf("pcf8563_getDateTime write error\r\n");
		return t;
    }

    /* As per data sheet, have to read everything all in one operation */
    uint8_t readBuffer[16] = {0};
	int ret = i2c_read_blocking_until(pcf8563_i2c, RTCC_ADDR, readBuffer, 16, false, make_timeout_time_ms(1000));
	if (ret == PICO_ERROR_GENERIC) {
		printf("pcf8563_getDateTime read error\r\n");
		return t;
	}
    //for (uint8_t i=0; i < 16; i++)
    //    readBuffer[i] = _i2c.read();

    // status bytes
    t.status1 = readBuffer[0];
    t.status2 = readBuffer[1];

    // time bytes
    //0x7f = 0b01111111
    t.volt_low = readBuffer[2] & RTCC_VLSEC_MASK;  //VL_Seconds
    t.sec = pcf8563_bcdToDec(readBuffer[2] & ~RTCC_VLSEC_MASK);
    t.min = pcf8563_bcdToDec(readBuffer[3] & 0x7f);
    //0x3f = 0b00111111
    t.hour = pcf8563_bcdToDec(readBuffer[4] & 0x3f);
    if(pcf8563_bcdToDec(readBuffer[4] & 0x3f) > 12) {
        t.hour12 = pcf8563_bcdToDec(readBuffer[4] & 0x3f) - 12;
        t.am = false;
    } else {
        t.hour12 = t.hour;
        t.am = true;
    }
    
    // date bytes
    //0x3f = 0b00111111
    t.day = pcf8563_bcdToDec(readBuffer[5] & 0x3f);
    //0x07 = 0b00000111
    t.weekday = pcf8563_bcdToDec(readBuffer[6] & 0x07);
    //get raw month data uint8_t and set month and century with it.
    t.month = readBuffer[7];
    if (t.month & RTCC_CENTURY_MASK)
        t.century = true;
    else
        t.century = false;
    //0x1f = 0b00011111
    t.month = t.month & 0x1f;
    t.month = pcf8563_bcdToDec(t.month);
    t.year = pcf8563_bcdToDec(readBuffer[8]);

    // alarm bytes
    t.alarm_min = readBuffer[9];
    if(0b10000000 & t.alarm_min)
        t.alarm_min = RTCC_NO_ALARM;
    else
        t.alarm_min = pcf8563_bcdToDec(t.alarm_min & 0b01111111);
    t.alarm_hour = readBuffer[10];
    if(0b10000000 & t.alarm_hour)
        t.alarm_hour = RTCC_NO_ALARM;
    else
        t.alarm_hour = pcf8563_bcdToDec(t.alarm_hour & 0b00111111);
    t.alarm_day = readBuffer[11];
    if(0b10000000 & t.alarm_day)
        t.alarm_day = RTCC_NO_ALARM;
    else
        t.alarm_day = pcf8563_bcdToDec(t.alarm_day  & 0b00111111);
    t.alarm_weekday = readBuffer[12];
    if(0b10000000 & t.alarm_weekday)
        t.alarm_weekday = RTCC_NO_ALARM;
    else
        t.alarm_weekday = pcf8563_bcdToDec(t.alarm_weekday  & 0b00000111);

    // CLKOUT_control 0x03 = 0b00000011
    t.squareWave = readBuffer[13] & 0x03;

    // timer bytes
    t.timer_control = readBuffer[14] & 0x03;
    t.timer_value = readBuffer[15];  // current value != set value when running

	return t;
}
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

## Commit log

2023-05-28 add kicad project
    [picowater.kicad_pcb, picowater.kicad_sch]
2023-05-28 update resistor
2023-06-03 add pico code (from pico_w example library)
2023-06-03 use lib for wifi + send udp beacon + flash led
2023-06-13 update PCB+code
    [picowater.kicad_pcb, picowater.kicad_sch]
2023-06-13 pcb update
    [picowater.kicad_pcb, picowater.kicad_sch]
2023-06-14 cleanup, use more uart output
2023-07-07 add infinite loop, start motor every 10 min
2023-07-12 use external RTC for wakeup
    [picowater.kicad_pcb, picowater.kicad_sch]
2023-07-14 update pcb
    [picowater.kicad_pcb, picowater.kicad_sch]
2023-07-29 [hw] update pcb
    [picowater.kicad_pcb, picowater.kicad_sch]
2023-07-29 handle water distance, humidity and cleanup/fixes
    [picowater.cpp]
2023-07-29 [hw] v0.3 release
    [picowater.kicad_pcb, picowater.kicad_sch]
2023-08-18 support for v0.3 PCB (non backward compatible) + add ssd1306 screen support
2024-03-17 [pcb] new 0.9 release with many changes
    - onboard DC-DC converter
    - onboard RTC
    - onboard Relay circuit
    - new connectors
    - others
    [picowater.kicad_pcb, picowater.kicad_sch]
2024-04-06 [pcb] fixes following v0.9
    [picowater.kicad_pcb]
2024-04-09 [pcb] fixes
    [picowater.kicad_pcb, picowater.kicad_sch]
2024-04-28 better use of the new rtc
    [picowater.kicad_pcb, picowater.kicad_sch]
2024-04-28 [pcb] add internal temp sensor
    [picowater.kicad_pcb, picowater.kicad_sch]
2024-04-28 fix humidity ADC
2024-05-01 working sockets (very basic)
2024-05-01 add server side php + fixes
    [picowater.cpp]
2025-03-29 [pcb] lots of fixes and simplification
    [picowater.kicad_pcb, picowater.kicad_sch]
2025-04-05 [hw] new PCB with RJ45 as connector and other changes + case
    [common.scad, picowater.kicad_pcb, picowater.kicad_sch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]
2025-04-05 [case] add stl
    [upssensor_bottom.stl, upssensor_top.stl]
2025-04-06 [case] add rj45, power jack and led holes
    [bottom.scad, bottom.stl, common.scad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]
2025-04-10 [case] adjust screw positions, minor tweaks
    [bottom.scad, bottom.stl, common.scad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]
2025-04-15 fw: send info to server, pcb: many tweaks
    [picowater.kicad_pcb, picowater.kicad_sch]
2025-05-25 [fw] change/add PINs for latest PCB
2025-05-25 [pcb] update
    [picowater.kicad_pcb, picowater.kicad_sch]
2025-05-29 [case] fix top cover
    [common.scad, top.scad, top.stl]
2025-05-29 [case] fixes + add internal battery holder
    [common.scad, top.scad, top.stl]
2025-06-08 [pcb] fix ADC + add internal connector for int. bat
    [picowater.kicad_pcb, picowater.kicad_sch]
2025-06-08 [case] fix screw size
    [bottom.scad, bottom.stl]
2025-06-11 [case] minor screws adjustment
    [bottom.scad, bottom.stl, top.scad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]
2025-06-15 [fw] add support for batlvl2, temperature, add failsafe
    [picowater.kicad_sch]
2025-11-23 [pcb] fix diode polarity on relay
    [picowater.kicad_pcb, picowater.kicad_sch]
2026-04-25 add sleep if no reboot, remove unused var
    [picowater.cpp]
